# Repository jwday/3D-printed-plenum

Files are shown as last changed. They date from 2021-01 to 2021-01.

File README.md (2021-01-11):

# 3D Printed Plenum for Cold Gas Propulsion
CAD model and description of 3D-printed plenum volume used in the development of a highly reliable cold gas propulsion system.

The plenum assembly (shown below) consists of the following components:
- 2x Plenum halves (yellow), (PLA, 0.35 mm diamater nozzle at 0.2 mm layer height)
- 1x 44 mm OD x 2 mm Nitrile O-ring
- 1x 44.5 mm ID O-ring holder, (PLA, 0.35 mm diamater nozzle at 0.2 mm layer height)
- 2x M5-to-1/8" threaded barbed fitting 
- 8x M2 x 0.4 x 16 mm SHCS
- 16x M2 flat washer
- 8x M2 x 0.4 hex nut

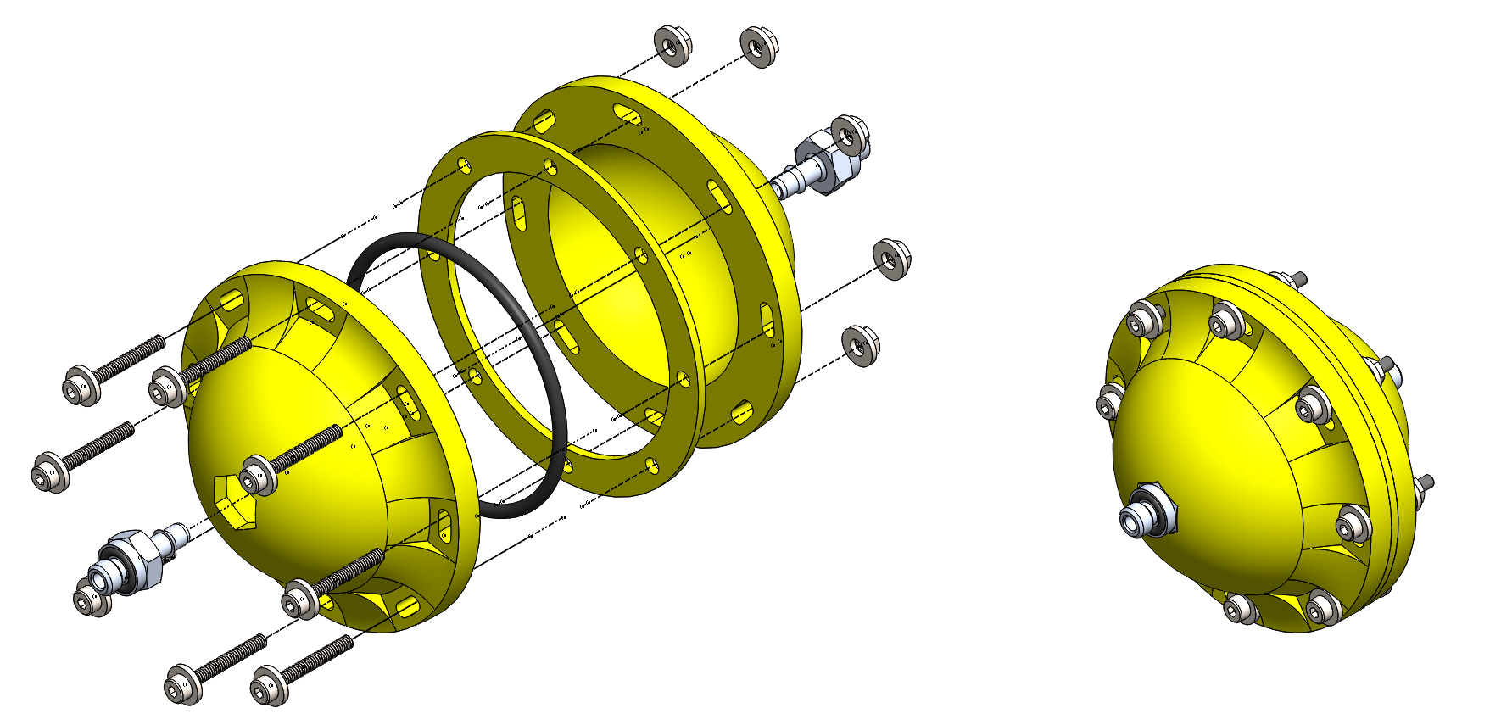
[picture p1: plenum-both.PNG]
Exploded plenum CAD model


The plenum halves are printed dome-side up with necessary support structure. Each plenum half is processed after printing with a round of sanding and epoxying, outlined as follows:

- Coarse sanding the inside with 100-grit sandpaper
- Marking orientation of plenum to M5-to-1/8" fitting to ensure final assembly is correctly aligned
- Mixing 2-part epoxy (Bob Smith Industries 30 minute slow-cure epoxy was used)
- Applying 2-part epoxy to interior of plenum with fitting held in place
- Allowing 24 hours for epoxy to cure
- Fine sanding the sealing surface with 400-grit sandpaper
- Finishing the sealing surface with wet sanding using 2000-grit wet sandpaper

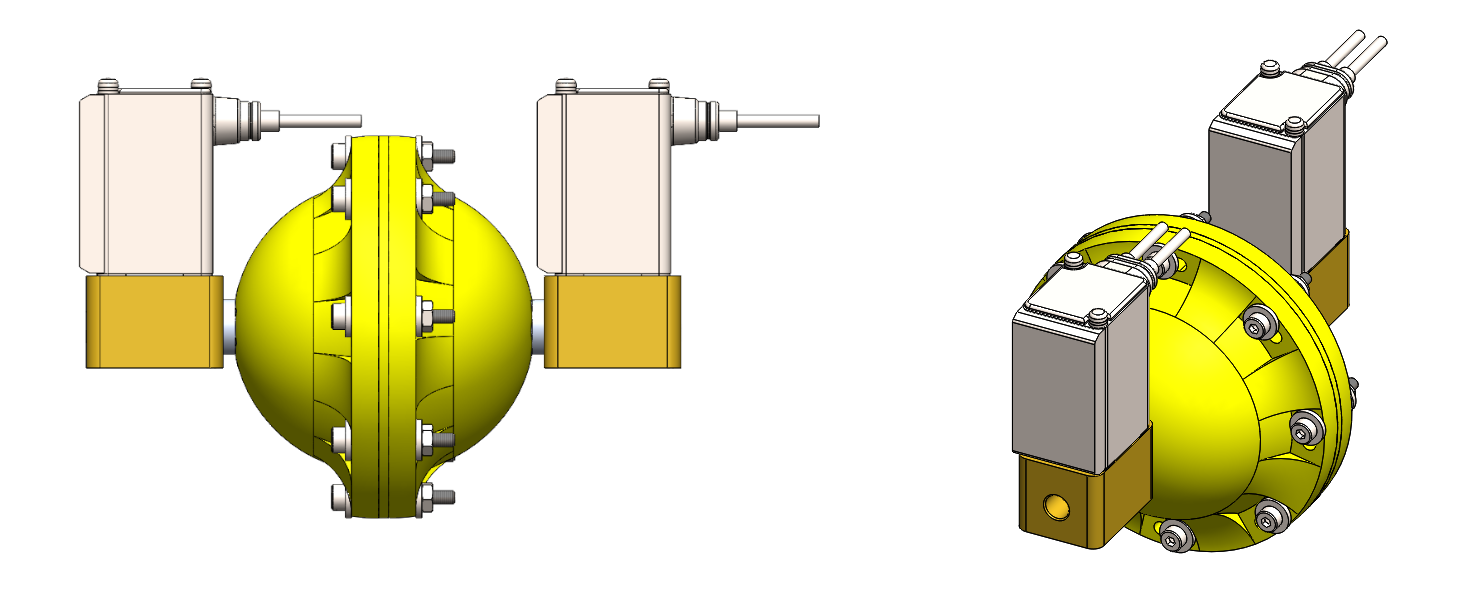
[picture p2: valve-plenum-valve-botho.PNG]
Plenum with valves assembled


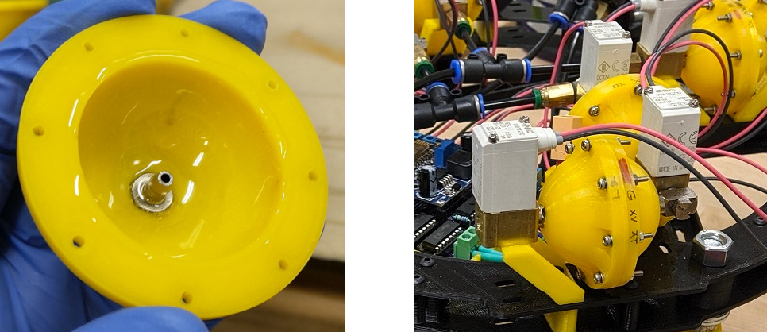
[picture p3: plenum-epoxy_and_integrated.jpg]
Plenum with valves assembled - real


Using a set of alignment jigs to hold the barbed fittings in place, the plenum assemblies could be sat dome-side down and allow the epoxy to pool to some degree at the bottom, further adhering the barbed fitting to the plenum structure and creating a strong, air-tight sealing surface. Once curing and wet sanding has taken place, the plenum can be assembled and pressurized.

The plenum was designed to operate nominally at 100 psi and was designed with a factor of safety of approximately 2.4. Multiple laboratory tests successfully held pressure at 200 psig (the maximum output of the regulator in use at the time). Eight full plenum assemblies were constructed with only one plenum half failing during proof testing.

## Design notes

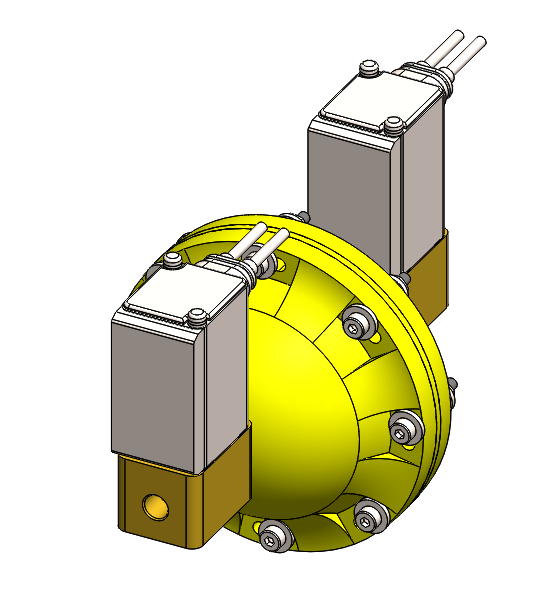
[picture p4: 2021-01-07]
valve-plenum-valve-iso.PNG

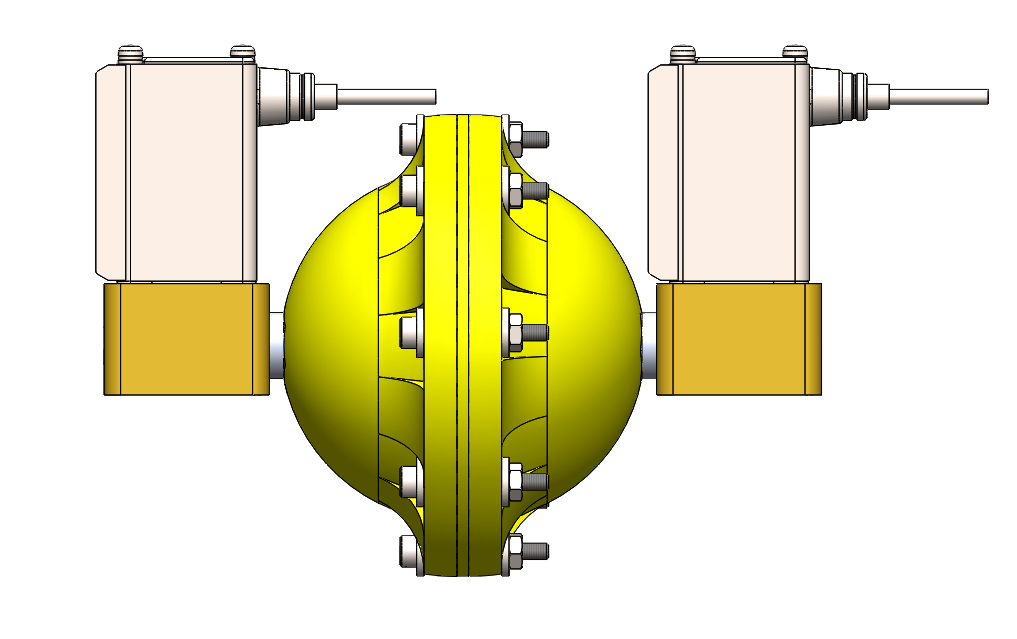
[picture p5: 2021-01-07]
valve-plenum-valve-side.PNG

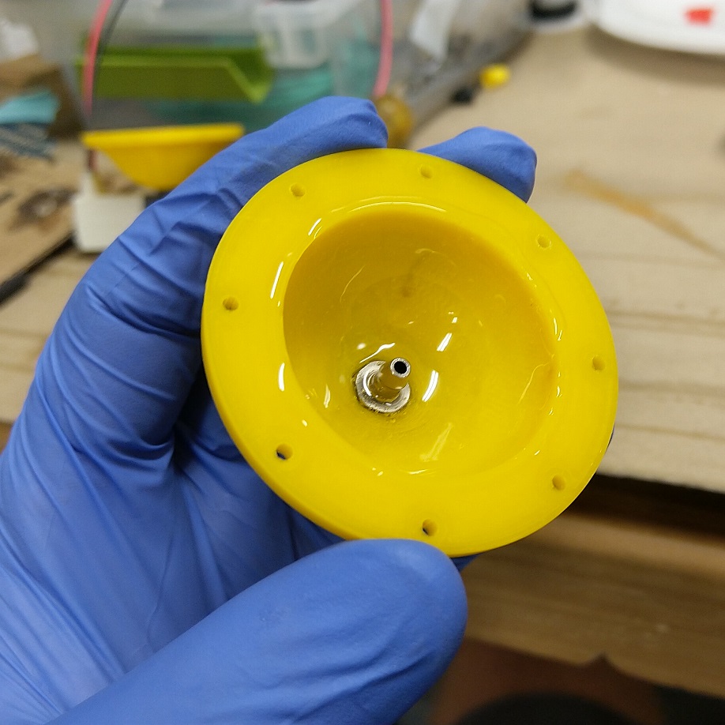
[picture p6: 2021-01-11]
plenum-epoxy_glove.jpg

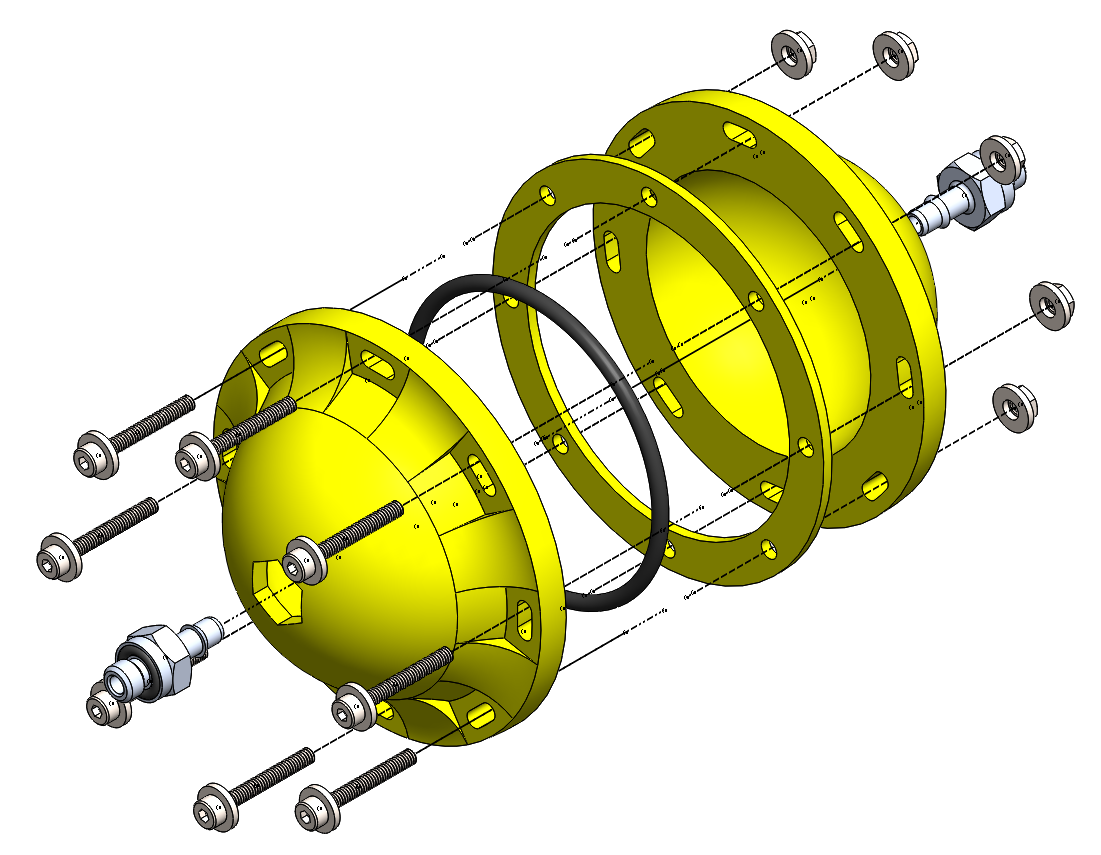
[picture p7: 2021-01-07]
plenum-exploded.PNG

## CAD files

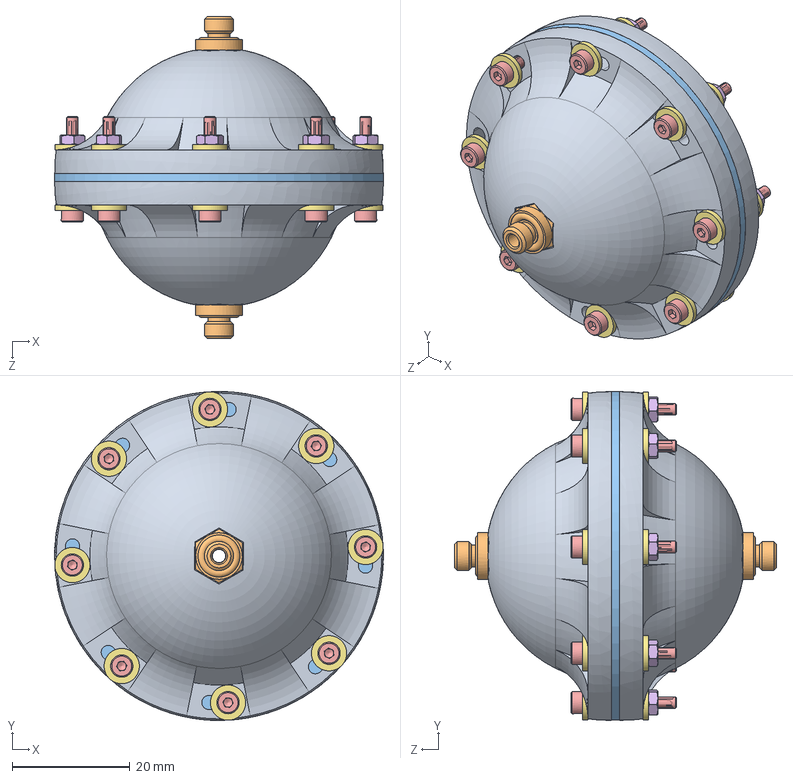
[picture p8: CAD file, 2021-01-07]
Plenum Assembly.SLDASM
56.0 x 56.0 x 54.8 mm
Plenum Half x 2
M5 to 1_8 in Threaded Barbed Fitting x 2
Oring Holder (44.5 mm ID, 1.4 mm Thick)
O-ring, 42 mm
socket head cap screw_am x 8
hex nut style 1_am x 8
flat washer regular_am x 16

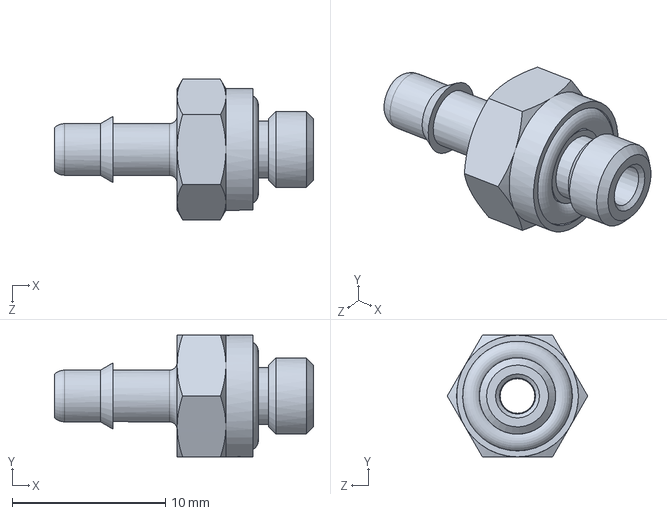
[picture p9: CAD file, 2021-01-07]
M5 to 1_8 in Threaded Barbed Fitting.SLDPRT
16.9 x 7.94 x 9.17 mm

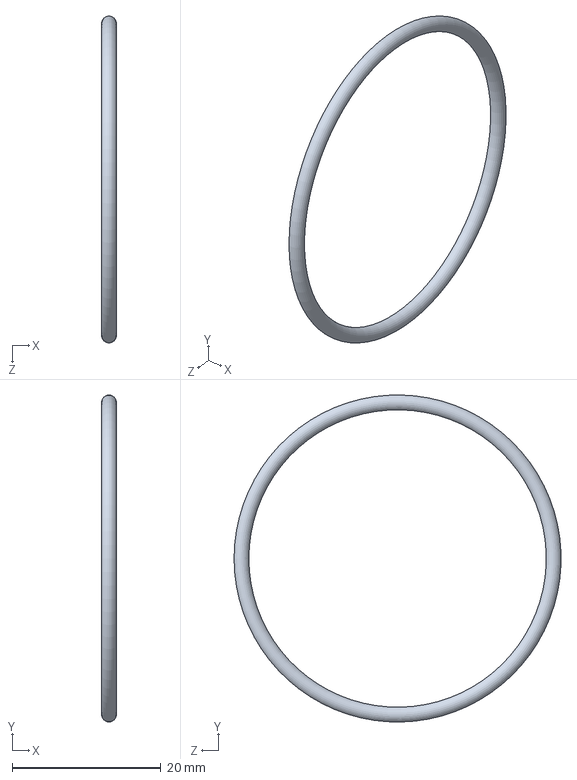
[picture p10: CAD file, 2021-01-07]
O-ring, 42 mm.SLDPRT
2.00 x 44.0 x 44.0 mm

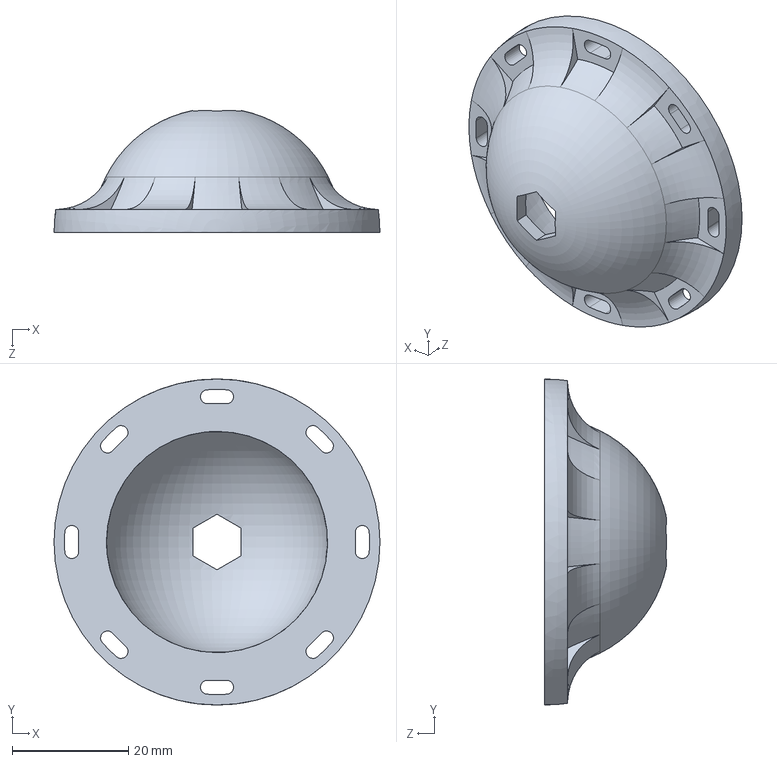
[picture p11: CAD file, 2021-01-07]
Plenum Half.SLDPRT
56.0 x 56.0 x 21.0 mm

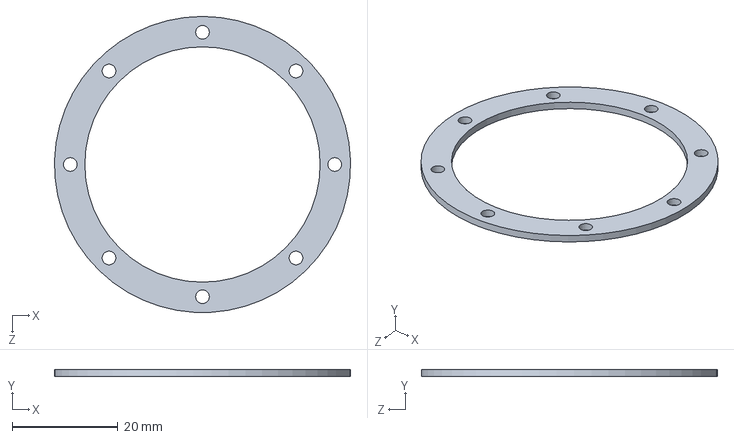
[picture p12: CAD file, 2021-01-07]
Oring Holder (44.5 mm ID, 1.4 mm Thick).SLDPRT
56.0 x 1.40 x 56.0 mm

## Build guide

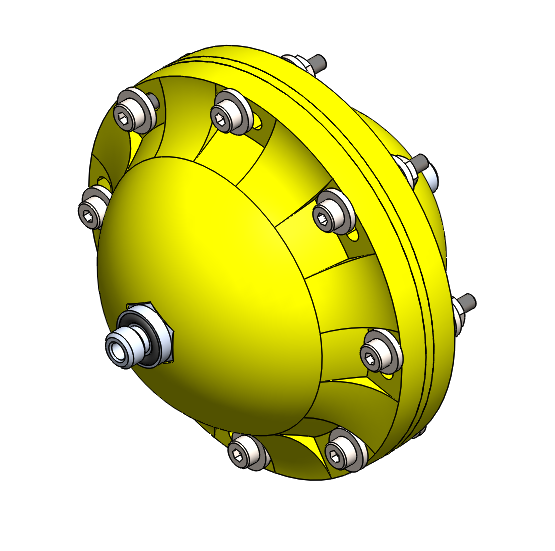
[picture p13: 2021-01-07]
plenum-assembled.PNG

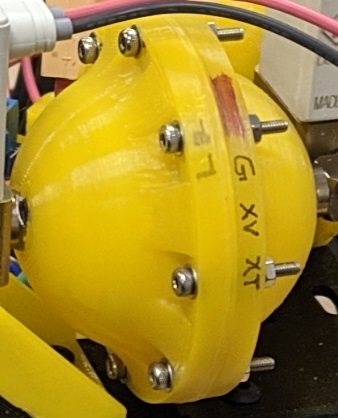
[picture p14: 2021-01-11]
plenum-assembled-real.jpg

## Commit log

2021-01-07 collapsed file structure
    [#10-32 to 1_8 in Threaded Barbed Fitting.SLDPRT, 4 mm Push-to-Connect to #10-32 UNF (McMaster-Carr 5779K244).SLDPRT, M-5UL.SLDASM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]
2021-01-07 updated barbed fitting from 10-32 to M5
    [#10-32 to 1_8 in Threaded Barbed Fitting.SLDPRT, M5 to 1_8 in Threaded Barbed Fitting.SLDPRT, Plenum Assembly.SLDASM]
2021-01-11 Added image of real assembled plenum
